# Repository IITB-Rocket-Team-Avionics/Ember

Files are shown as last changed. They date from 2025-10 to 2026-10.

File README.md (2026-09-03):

# Ember
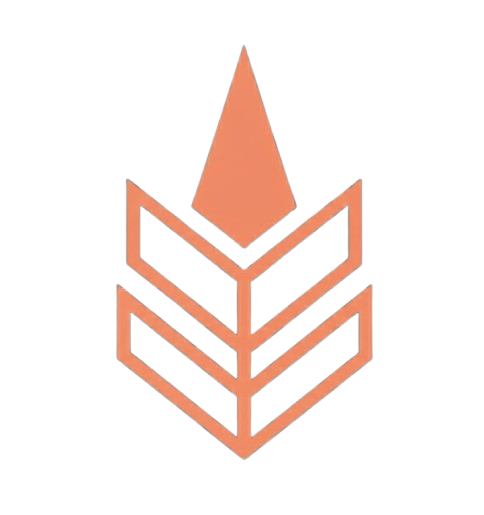
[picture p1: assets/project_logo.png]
Project Logo


Ember is the SRAD flight computer system of the IITB Rocket Team, developed as an experimental platform with mitigations for issues faced by previous systems and as a testbed for new avionics architecture.

## Version Descriptions

### Ember Pilot
Proof of concept version validating new LoRa telemetry and core sensor suite. Features a Raspberry Pi Pico 2 dev board instead of a bare-metal hardware design. All systems validated for future versions.

| Parameter | Details |
|---|---|
| MCU | RP2350A (Pico 2 dev board) |
| Layers | 4 |
| Sensors | BMP280, BNO055, KX134 |
| GNSS | Teseo LIV3F |
| Telemetry | Waveshare Core SX1262 (920MHz LoRa) |

---

### Ember V0.2 (Ember)
First full flight version. Flew successfully at IREC 2026, reaching an apogee of 9,463 ft with a SRAD N-class KNSB motor — 2% overshoot on OpenRocket predicted apogee of 9,272 ft. Split into two boards: Flight Computer Unit (FCU) and Telemetry & Data Unit (TDU).

| Parameter | Details |
|---|---|
| FCU MCU | RP2350A (Pico 2 dev board) |
| TDU MCU | RP2350A (Pico 2 dev board) |
| Layers | 2 |
| Sensors | BMP280, BNO055, KX134, NXP MPXV5100DP |
| GNSS | Quectel L89HA (multi-constellation) |
| Telemetry | Waveshare Core1262 SX1262 (920MHz LoRa) |
| Recovery | Dual deploy — drogue at apogee, main at 400m AGL |
| Pyro channels | 4 (2 primary, 2 redundant) |
| Data logging | External flash |
| COTS backup | EasyMini V2 |

---

### Ember V1 (In Development)
Major architectural redesign with full separation of concerns across dedicated board types. Introduces triple modular redundant recovery, distributed CAN bus architecture, and significantly upgraded data acquisition.

**Board types:**

**NTDU (Navigation, Telemetry & Data Unit)** — main board. Independent sensor suite for navigation and state estimation, GNSS, LoRa telemetry, data acquisition (dp probe, strain gauges), configuration authority for all nodes on boot, aggregates and logs data from all CAN nodes.

| Parameter | Details |
|---|---|
| MCU | STM32H573 |
| Sensors | BMP384, BNO055, KX134, NXP MPXV5100DP (via ADS1220), BX350-3AA strain gauges (via ADS1220) |
| GNSS | Quectel L89HA |
| Telemetry | SX1262 920MHz LoRa |
| Data logging | OctoSPI NOR flash + microSD |
| Communication | CAN bus (all nodes) |
| Power | 2S Li-ion, AP63205WU buck (5V) |

**RU (Recovery Unit) — x3** — dedicated recovery boards in triple modular redundant configuration. Distributed 2-of-3 voting via CAN bus. Each board independently detects apogee and participates in consensus voting.

| Parameter | Details |
|---|---|
| MCU | STM32F411 |
| Sensors | BMP280, single-axis accelerometer |
| Pyro channels | 2 (drogue + main) |
| Communication | CAN bus (shared with NTDU) |
| RTOS | FreeRTOS |
| Power | 1S Li-ion (isolated per board) |
| Voting | 2-of-3 mid-value select consensus |

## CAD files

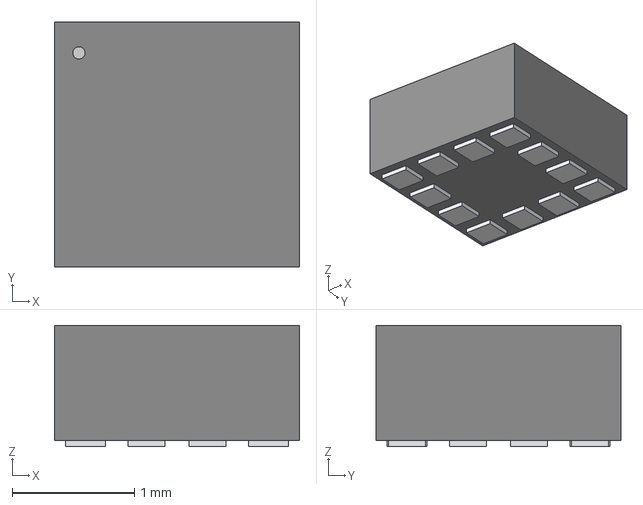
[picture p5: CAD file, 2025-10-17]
EDA_libraries/LGA12_2X2X0P9_ROM.step
2.01 x 2.01 x 0.993 mm

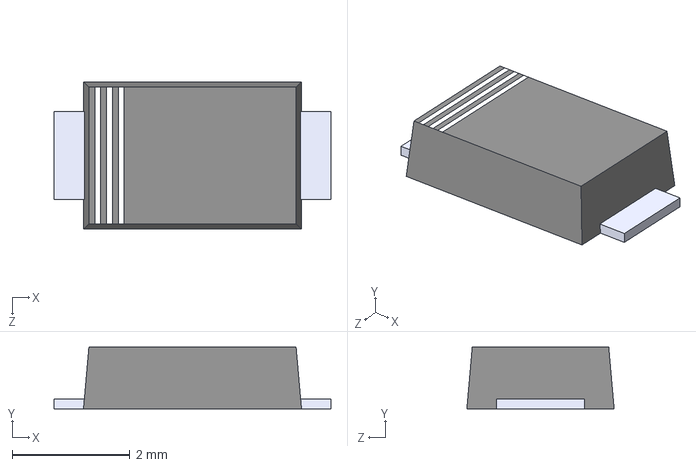
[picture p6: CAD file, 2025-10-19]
EDA_libraries/RSX501LAM20TR/RSX501LAM20TR.step
4.70 x 1.05 x 2.50 mm

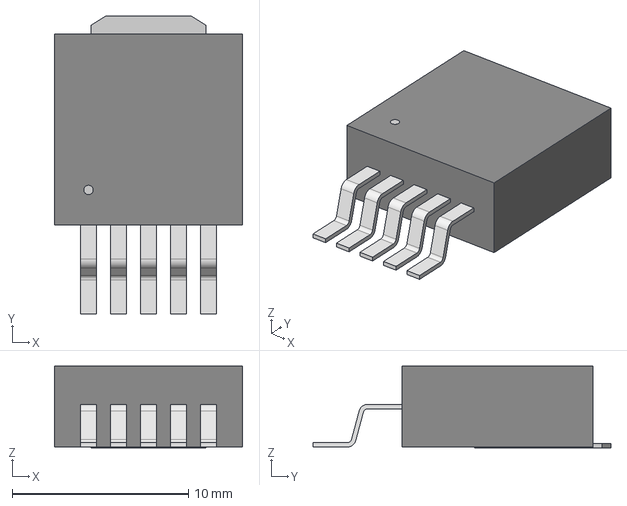
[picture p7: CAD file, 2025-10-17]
EDA_libraries/TO-263-5_MCH.step
10.7 x 16.9 x 4.65 mm

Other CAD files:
assets/project_logo.dxf

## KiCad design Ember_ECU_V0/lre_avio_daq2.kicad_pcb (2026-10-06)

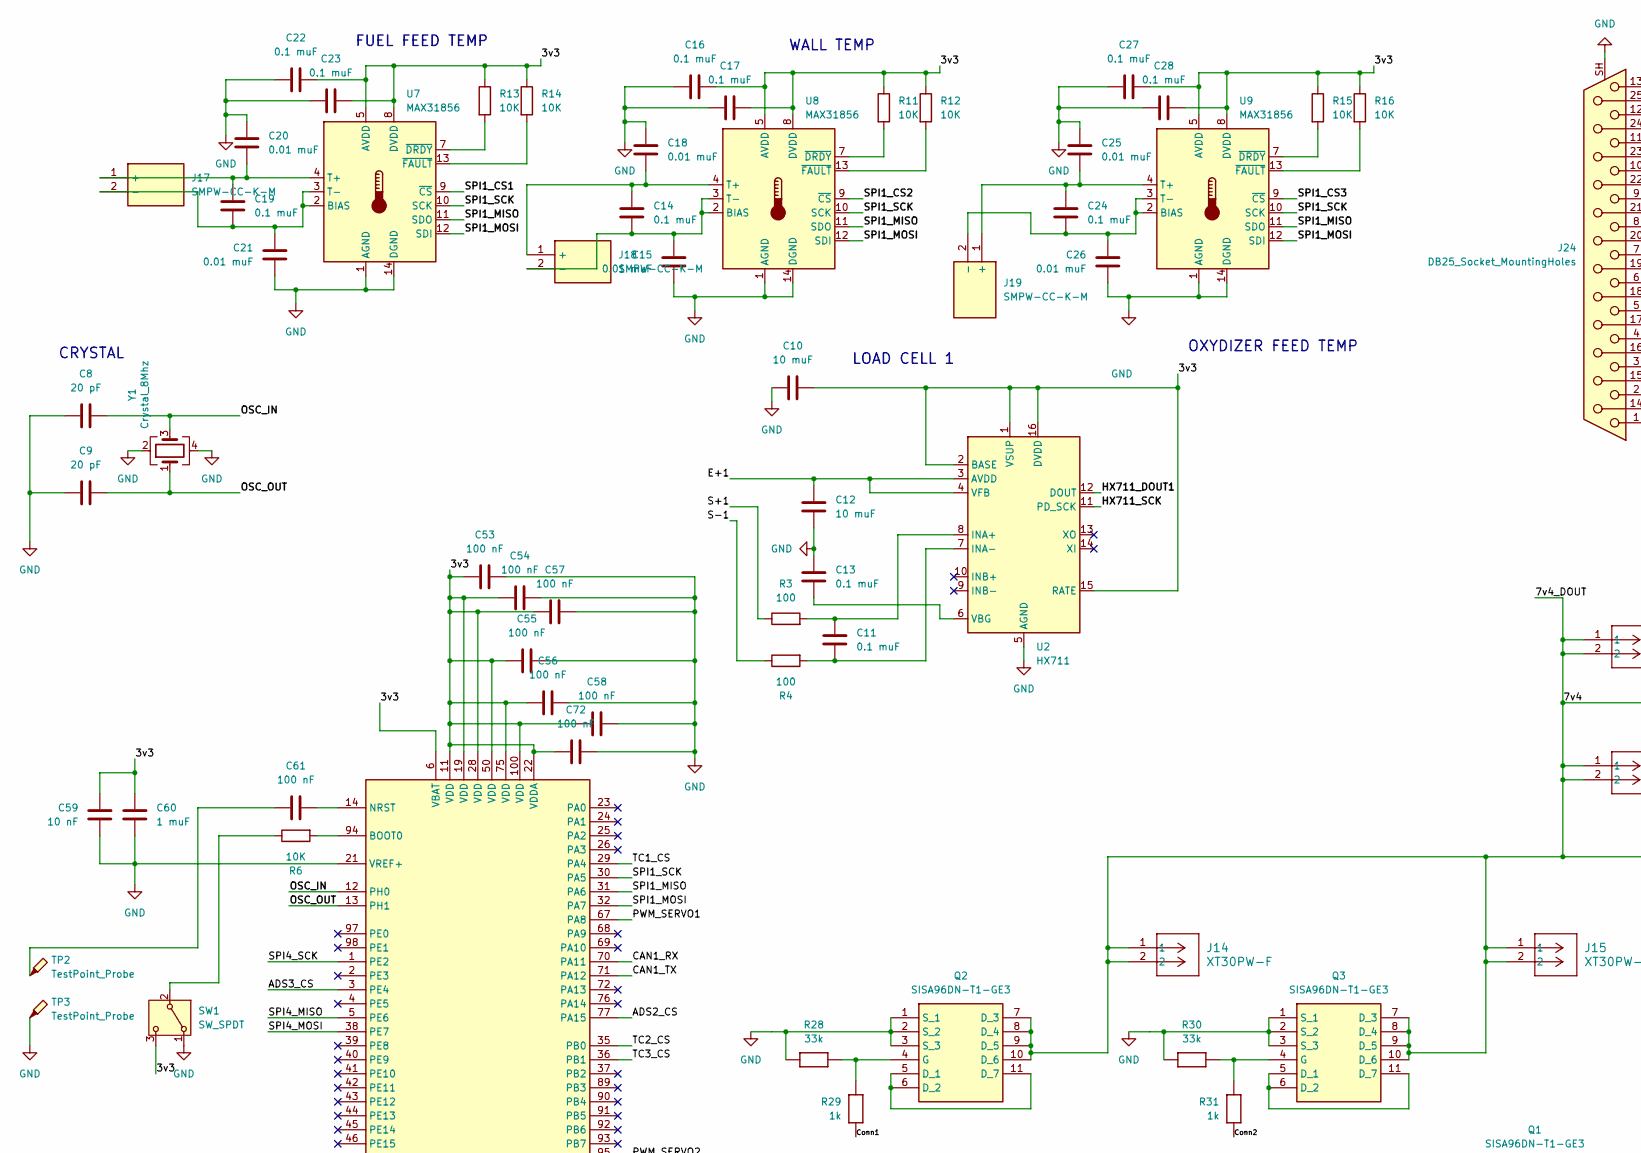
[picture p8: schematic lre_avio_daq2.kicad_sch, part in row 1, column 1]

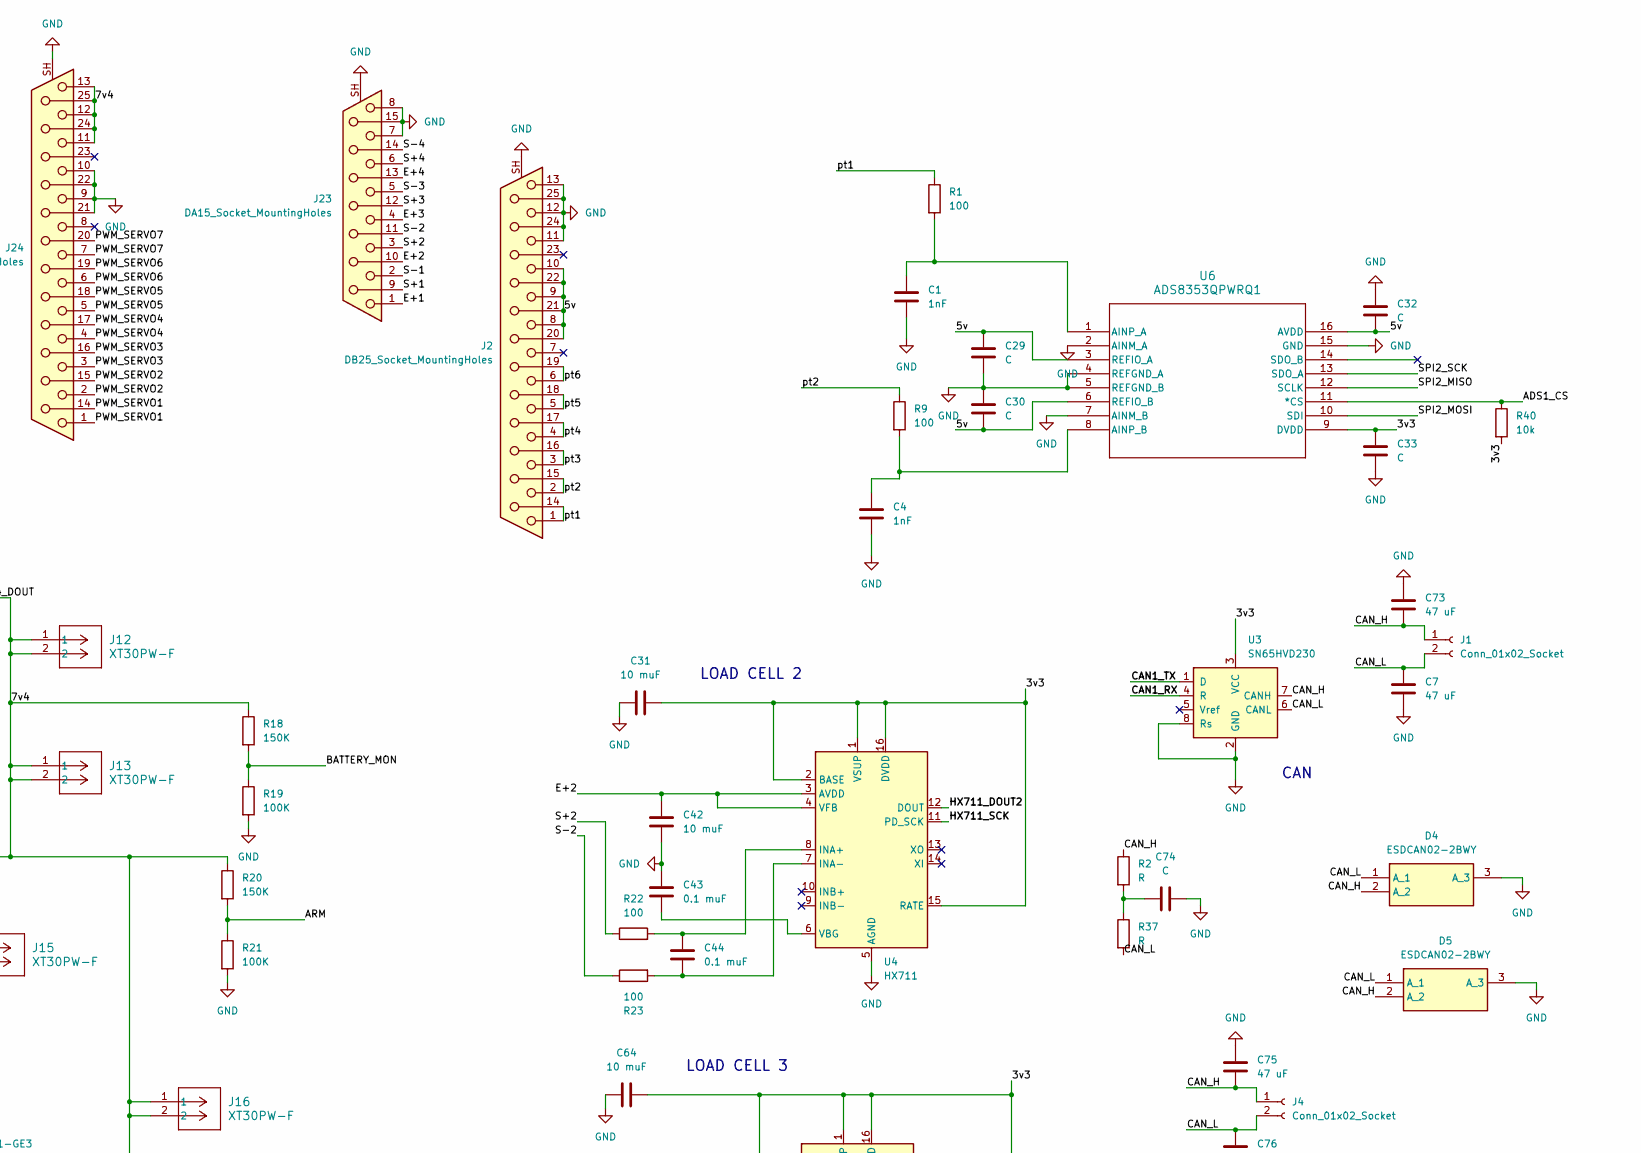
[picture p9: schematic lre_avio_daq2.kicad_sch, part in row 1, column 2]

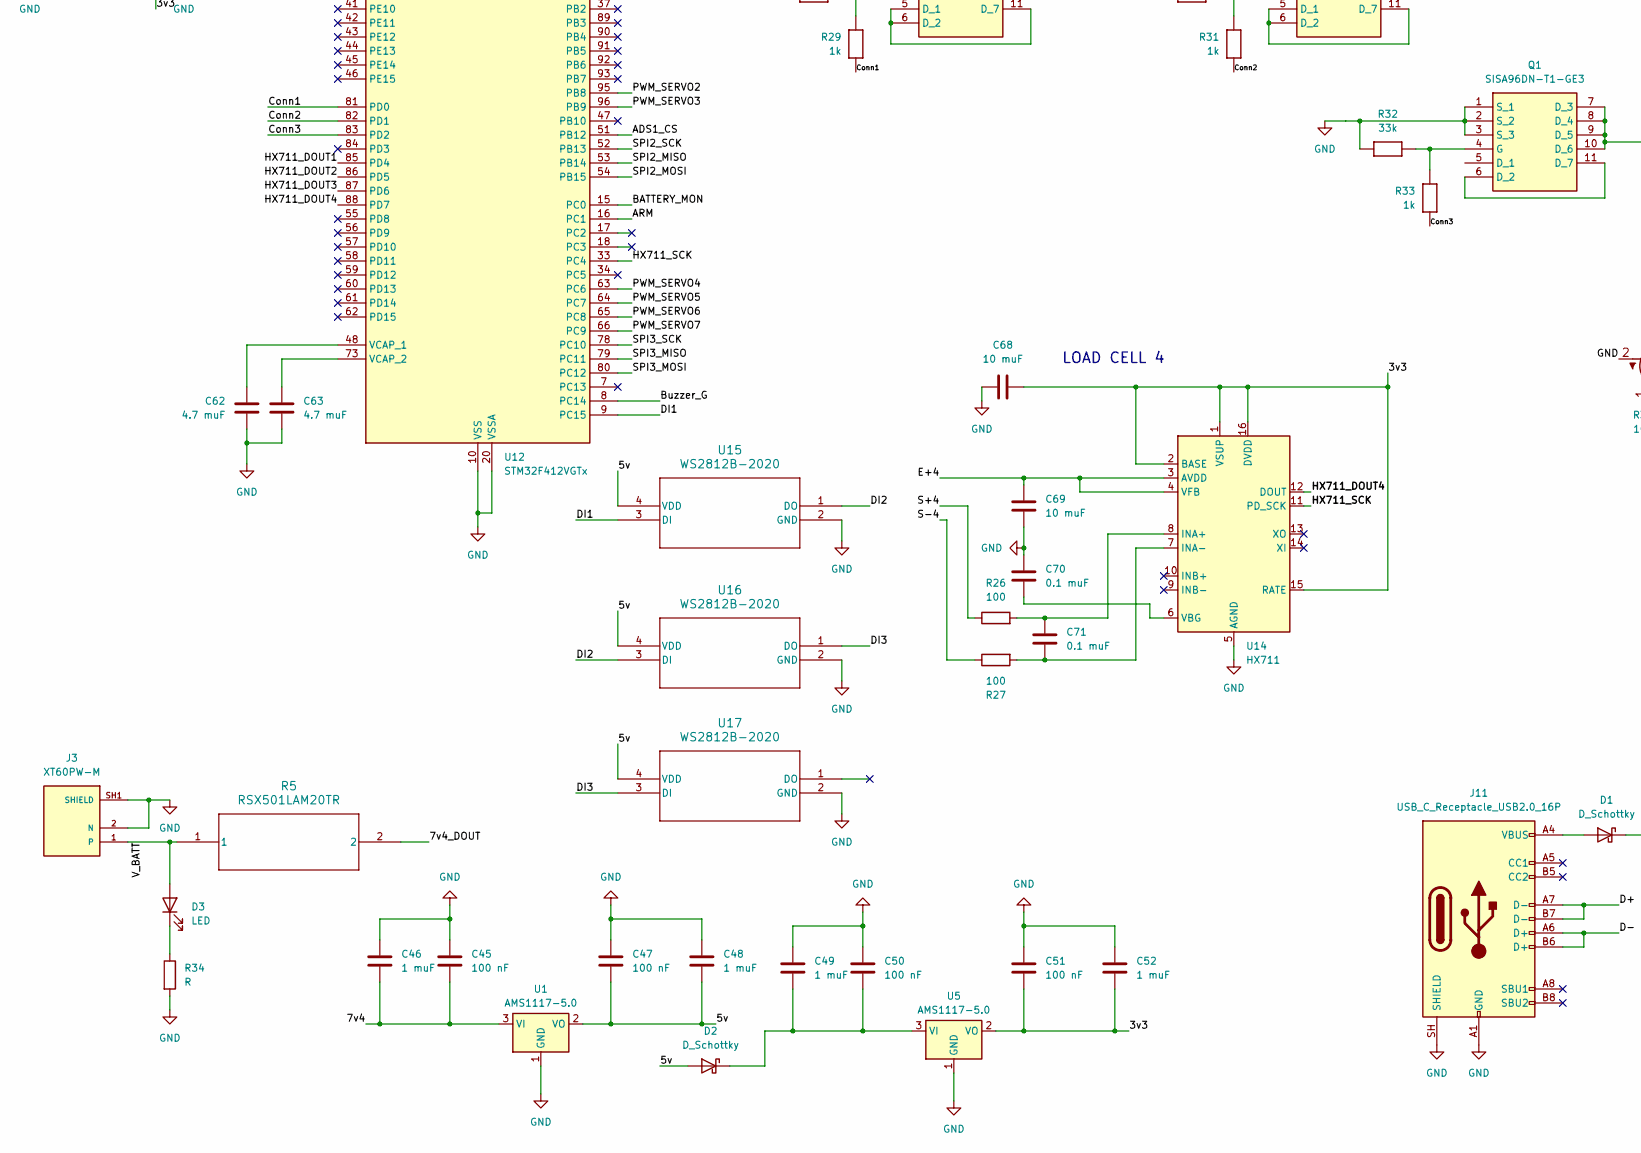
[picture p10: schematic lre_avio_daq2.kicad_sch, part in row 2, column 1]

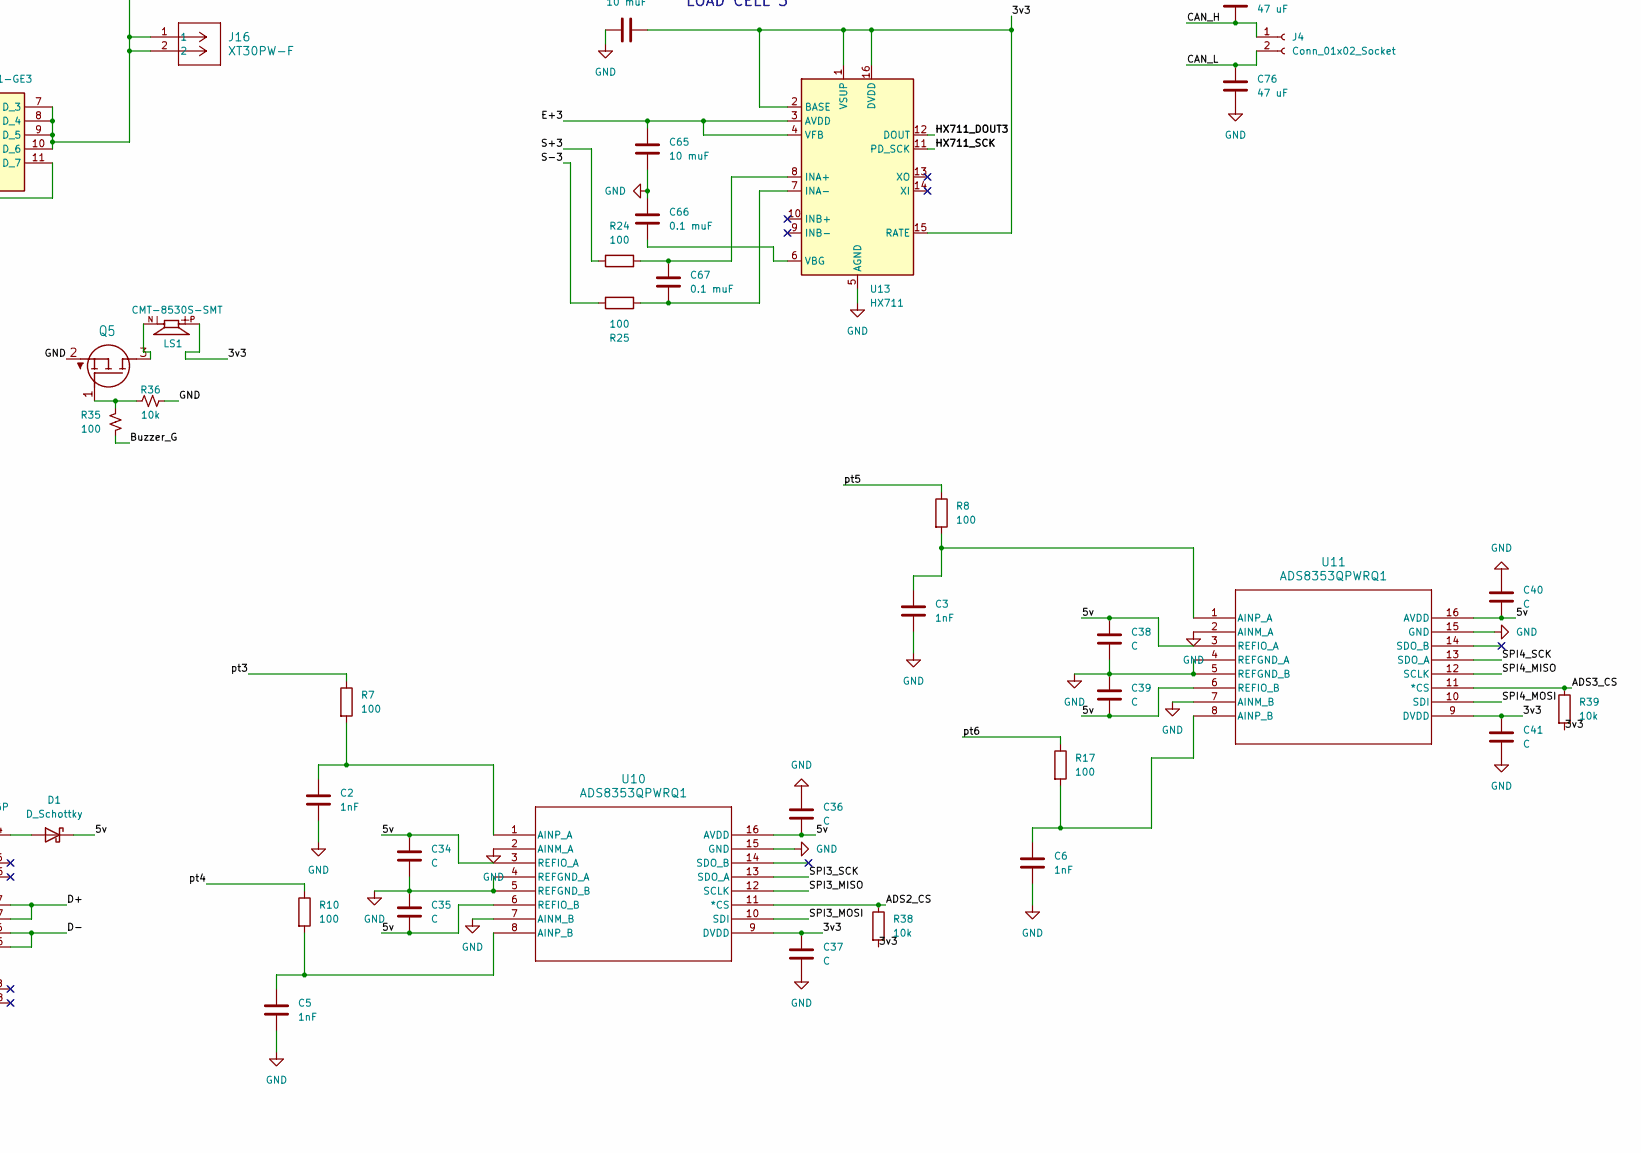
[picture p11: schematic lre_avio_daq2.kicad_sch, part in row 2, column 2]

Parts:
C1, C2, C3, C4, C5, C6: 1nF; C_0603_1608Metric
C7, C73, C75, C76: 47 uF; C_0603_1608Metric
C8, C9: 20 pF; C_0603_1608Metric
C10, C12, C31, C42, C64, C65, C68, C69: 10 muF; C_0603_1608Metric
C11, C13, C14, C16, C17, C19, C22, C23, C24, C27, C28, C43, C44, C66, C67, C70, C71: 0.1 muF; C_0603_1608Metric
C15, C18, C20, C21, C25, C26: 0.01 muF; C_0603_1608Metric
C29, C30, C32, C33, C34, C35, C36, C37, C38, C39, C40, C41, C74: C; C_0603_1608Metric
C45, C47, C50, C51, C53, C54, C55, C56, C57, C58, C61, C72: 100 nF; C_0603_1608Metric
C46, C48, C49, C52, C60: 1 muF; C_0603_1608Metric
C59: 10 nF; C_0603_1608Metric
C62, C63: 4.7 muF; C_0603_1608Metric
D1, D2: D_Schottky; DIO_RB050LAM_ROM
D3: LED; LED_0603_1608Metric
D4, D5: ESDCAN02-2BWY; SOT65P210X110-3N; Manufacturer_Part_Number ESDCAN02-2BWY; Mouser Part Number 511-ESDCAN02-2BWY
J1, J4: Conn_01x02_Socket; JST_EH_B2B-EH-A_1x02_P2.50mm_Vertical
J2, J24: DB25_Socket_MountingHoles; DSUB-25_Socket_Horizontal_P2.77x2.84mm_EdgePinOffset4.94mm_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
J3: XT60PW-M; AMASS_XT60PW-M; PARTREV 1.2
J11: USB_C_Receptacle_USB2.0_16P; USB_C_Receptacle_Amphenol_12401948E412A
J12, J13, J14, J15, J16: XT30PW-F; CONN_XT30PW-F_AMA
J17, J18, J19: SMPW-CC-K-M; SMPWCCKM; Manufacturer_Part_Number SMPW-CC-K-M
J23: DA15_Socket_MountingHoles; DSUB-15_Socket_Horizontal_P2.77x2.84mm_EdgePinOffset4.94mm_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
LS1: CMT-8530S-SMT; CUI_CMT-8530S-SMT
Q1, Q2, Q3: SISA96DN-T1-GE3; SIS862DNT1GE3; Manufacturer_Part_Number SISA96DN-T1-GE3; Mouser Part Number 78-SISA96DN-T1-GE3
Q5: SOT95P240X115-3N
R1, R3, R4, R7, R8, R9, R10, R17, R22, R23, R24, R25, R26, R27, R35: 100; R_0603_1608Metric
R2, R34, R37: R; R_0603_1608Metric
R5: RSX501LAM20TR; R_0603_1608Metric
R6, R11, R12, R13, R14, R15, R16: 10K; R_0603_1608Metric
R18, R20: 150K; R_0603_1608Metric
R19, R21: 100K; R_0603_1608Metric
R28, R30, R32: 33k; R_0603_1608Metric
R29, R31, R33: 1k; R_0603_1608Metric
R36, R38, R39, R40: 10k; R_0603_1608Metric
SW1: SW_SPDT; SW_SPDT_PCM12
TP2, TP3: TestPoint_Probe; TestPoint_Pad_D1.5mm
U1, U5: AMS1117-5.0; SOT-223-3_TabPin2
U2, U4, U13, U14: HX711; SOIC-16_3.9x9.9mm_P1.27mm
U3: SN65HVD230; SOIC-8_3.9x4.9mm_P1.27mm
U6, U10, U11: ADS8353QPWRQ1; TSSOP16_PW_TEX-L
U7, U8, U9: MAX31856; TSSOP-14_4.4x5mm_P0.65mm
U12: STM32F412VGTx; LQFP-100_14x14mm_P0.5mm
U15, U16, U17: WS2812B-2020; SMT_12B-2020_WDS
Y1: Crystal_8Mhz; Crystal_SMD_7050-4Pin_7.0x5.0mm

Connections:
/3v3: C10.2, C16.2, C17.2, C22.2, C23.2, C27.2, C28.2, C31.2, C33.1, C37.1, C41.1, C51.2, C52.2, C53.1, C54.1, C55.1, C56.1, C57.1, C58.1, C59.1, C60.1, C64.2, C68.2, C72.2, LS1.P, R11.1, R12.1, R13.1, R14.1, R15.1, R16.1, R38.2, R39.2, R40.2, SW1.3 (C), U2.1 (VSUP), U2.2 (BASE), U2.15 (RATE), U2.16 (DVDD), U3.3 (VCC), U4.1 (VSUP), U4.2 (BASE), U4.15 (RATE), U4.16 (DVDD), U5.2 (VO), U6.9 (DVDD), U7.5 (AVDD), U7.8 (DVDD), U8.5 (AVDD), U8.8 (DVDD), U9.5 (AVDD), U9.8 (DVDD), U10.9 (DVDD), U11.9 (DVDD), U12.6 (VBAT), U12.11 (VDD), U12.19 (VDD), U12.22 (VDDA), U12.28 (VDD), U12.50 (VDD), U12.75 (VDD), U12.100 (VDD), U13.1 (VSUP), U13.2 (BASE), U13.15 (RATE), U13.16 (DVDD), U14.1 (VSUP), U14.2 (BASE), U14.15 (RATE), U14.16 (DVDD)
/5v: C29.2, C30.2, C32.2, C34.2, C35.2, C36.2, C38.2, C39.2, C40.2, C47.2, C48.2, D1.1 (K), D2.2 (A), J2.8, J2.9, J2.10, J2.20, J2.21, J2.22, U1.2 (VO), U6.3 (REFIO_A), U6.6 (REFIO_B), U6.16 (AVDD), U10.3 (REFIO_A), U10.6 (REFIO_B), U10.16 (AVDD), U11.3 (REFIO_A), U11.6 (REFIO_B), U11.16 (AVDD), U15.4 (VDD), U16.4 (VDD), U17.4 (VDD)
/7v4: C45.2, C46.2, J12.1, J12.2, J13.1, J13.2, J14.1, J14.2, J15.1, J15.2, J16.1, J16.2, J24.11, J24.12, J24.13, J24.24, J24.25, Q1.7 (D_3), Q1.8 (D_4), Q1.9 (D_5), Q1.10 (D_6), Q2.7 (D_3), Q2.8 (D_4), Q2.9 (D_5), Q2.10 (D_6), Q3.7 (D_3), Q3.8 (D_4), Q3.9 (D_5), Q3.10 (D_6), R5.2, R18.1, R20.1, U1.3 (VI)
/ADS1_CS: R40.1, U6.11 (*CS), U12.51 (PB12)
/ADS2_CS: R38.1, U10.11 (*CS), U12.77 (PA15)
/ADS3_CS: R39.1, U11.11 (*CS), U12.3 (PE4)
/ARM: R20.2, R21.1, U12.16 (PC1)
/BATTERY_MON: R18.2, R19.1, U12.15 (PC0)
/Buzzer_G: R35.2, U12.8 (PC14)
/CAN1_RX: U3.4 (R), U12.70 (PA11)
/CAN1_TX: U3.1 (D), U12.71 (PA12)
/CAN_L: C7.1, C76.1, D4.1 (A_1), D5.1 (A_1), J1.2, J4.2, R37.2, U3.6 (CANL)
/Conn1: R29.1, U12.81 (PD0)
/Conn2: R31.1, U12.82 (PD1)
/Conn3: R33.1, U12.83 (PD2)
/D+: J11.A7 (D-), J11.B7 (D-)
/D-: J11.A6 (D+), J11.B6 (D+)
/DI1: U12.9 (PC15), U15.3 (DI)
/DI2: U15.1 (DO), U16.3 (DI)
/DI3: U16.1 (DO), U17.3 (DI)
/E+1: C12.1, J23.1, U2.3 (AVDD), U2.4 (VFB)
/E+2: C42.1, J23.10, U4.3 (AVDD), U4.4 (VFB)
/E+3: C65.1, J23.4, U13.3 (AVDD), U13.4 (VFB)
/E+4: C69.1, J23.13, U14.3 (AVDD), U14.4 (VFB)
/HX711_DOUT1: U2.12 (DOUT), U12.85 (PD4)
/HX711_DOUT2: U4.12 (DOUT), U12.86 (PD5)
/HX711_DOUT3: U12.87 (PD6), U13.12 (DOUT)
/HX711_DOUT4: U12.88 (PD7), U14.12 (DOUT)
/HX711_SCK: U2.11 (PD_SCK), U4.11 (PD_SCK), U12.33 (PC4), U13.11 (PD_SCK), U14.11 (PD_SCK)
/OSC_IN: C8.2, U12.12 (PH0), Y1.3
/OSC_OUT: C9.2, U12.13 (PH1), Y1.1
/PWM_SERVO1: J24.1, J24.14, U12.67 (PA8)
/PWM_SERVO2: J24.2, J24.15, U12.95 (PB8)
/PWM_SERVO3: J24.3, J24.16, U12.96 (PB9)
/PWM_SERVO4: J24.4, J24.17, U12.63 (PC6)
/PWM_SERVO5: J24.5, J24.18, U12.64 (PC7)
/PWM_SERVO6: J24.6, J24.19, U12.65 (PC8)
/PWM_SERVO7: J24.7, J24.20, U12.66 (PC9)
/S+1: J23.9, R3.1
/S+2: J23.3, R22.1
/S+3: J23.12, R24.1
/S+4: J23.6, R26.1
/S-1: J23.2, R4.1
/S-2: J23.11 (P111), R23.1
/S-3: J23.5, R25.1
/S-4: J23.14, R27.1
/SPI1_CS1: U7.9 (~CS)
/SPI1_CS2: U8.9 (~CS)
/SPI1_CS3: U9.9 (~CS)
/SPI1_MISO: U7.11 (SDO), U8.11 (SDO), U9.11 (SDO), U12.31 (PA6)
/SPI1_MOSI: U7.12 (SDI), U8.12 (SDI), U9.12 (SDI), U12.32 (PA7)
/SPI1_SCK: U7.10 (SCK), U8.10 (SCK), U9.10 (SCK), U12.30 (PA5)
/SPI2_MISO: U6.12 (SCLK), U12.53 (PB14)
/SPI2_MOSI: U6.10 (SDI), U12.54 (PB15)
/SPI2_SCK: U6.13 (SDO_A), U12.52 (PB13)
/SPI3_MISO: U10.12 (SCLK), U12.79 (PC11)
/SPI3_MOSI: U10.10 (SDI), U12.80 (PC12)
/SPI3_SCK: U10.13 (SDO_A), U12.78 (PC10)
/SPI4_MISO: U11.12 (SCLK), U12.5 (PE6)
/SPI4_MOSI: U11.10 (SDI), U12.38 (PE7)
/SPI4_SCK: U11.13 (SDO_A), U12.1 (PE2)
/TC1_CS: U12.29 (PA4)
/TC2_CS: U12.35 (PB0)
/TC3_CS: U12.36 (PB1)
/V_BATT: D3.2 (A), J3.1, R5.1
/pt1: J2.1, J2.14, R1.1
/pt2: J2.2, J2.15, R9.1
/pt3: J2.3, J2.16, R7.1
/pt4: J2.4, J2.17, R10.1
/pt5: J2.5, J2.18, R8.1
/pt6: J2.6, J2.19, R17.1
GND: C1.2, C2.2, C3.2, C4.2, C5.2, C6.2, C7.2, C8.1, C9.1, C10.1, C12.2, C13.1, C15.2, C16.1, C17.1, C18.1, C20.1, C21.2, C22.1, C23.1, C25.1, C26.2, C27.1, C28.1, C29.1, C30.1, C31.1, C32.1, C33.2, C34.1, C35.1, C36.1, C37.2, C38.1, C39.1, C40.1, C41.2, C42.2, C43.1, C45.1, C46.1, C47.1, C48.1, C49.1, C50.1, C51.1, C52.1, C53.2, C54.2, C55.2, C56.2, C57.2, C58.2, C59.2, C60.2, C62.2, C63.2, C64.1, C65.2, C66.1, C68.1, C69.2, C70.1, C72.1, C73.1, C74.2, C75.1, C76.2, D4.3 (A_3), D5.3 (A_3), J2.11, J2.12, J2.13, J2.24, J2.25, J2.SH (PAD), J3.2 (N), J3.SH1 (SHIELD), J3.SH2 (SHIELD), J11.A1 (GND), J11.A12 (GND), J11.B1 (GND), J11.B12 (GND), J11.SH (SHIELD), J23.7, J23.8, J23.15, J23.SH (PAD), J24.9, J24.10, J24.21, J24.22, J24.SH (PAD), Q1.1 (S_1), Q1.2 (S_2), Q1.3 (S_3), Q2.1 (S_1), Q2.2 (S_2), Q2.3 (S_3), Q3.1 (S_1), Q3.2 (S_2), Q3.3 (S_3), Q5.2 (S), R19.2, R21.2, R28.2, R30.2, R32.2, R34.2, R36.1, SW1.1 (A), TP3.1 (1_1), U1.1 (GND), U2.5 (AGND), U3.2 (GND), U3.8 (Rs), U4.5 (AGND), U5.1 (GND), U6.2 (AINM_A), U6.4 (REFGND_A), U6.5 (REFGND_B), U6.7 (AINM_B), U6.15 (GND), U7.1 (AGND), U7.14 (DGND), U8.1 (AGND), U8.14 (DGND), U9.1 (AGND), U9.14 (DGND), U10.2 (AINM_A), U10.4 (REFGND_A), U10.5 (REFGND_B), U10.7 (AINM_B), U10.15 (GND), U11.2 (AINM_A), U11.4 (REFGND_A), U11.5 (REFGND_B), U11.7 (AINM_B), U11.15 (GND), U12.10 (VSS), U12.20 (VSSA), U12.21 (VREF+), U12.27 (VSS), U12.49 (VSS), U12.74 (VSS), U12.99 (VSS), U13.5 (AGND), U14.5 (AGND), U15.2 (GND), U16.2 (GND), U17.2 (GND), Y1.2, Y1.4
unnamed: C61.1, TP2.1 (1_1)
unnamed: D1.2 (A), J11.A4 (VBUS), J11.A9 (VBUS), J11.B4 (VBUS), J11.B9 (VBUS)
unnamed: C49.2, C50.2, D2.1 (K), U5.3 (VI)
unnamed: D3.1 (K), R34.1
unnamed: C19.1, C20.2, J17.1 (+), U7.4 (T+)
unnamed: C19.2, C21.1, J17.2 (-), U7.2 (BIAS), U7.3 (T-)
unnamed: C14.1, C18.2, J18.1 (+), U8.4 (T+)
unnamed: C14.2, C15.1, J18.2 (-), U8.2 (BIAS), U8.3 (T-)
unnamed: C24.1, C25.2, J19.1 (+), U9.4 (T+)
unnamed: C24.2, C26.1, J19.2 (-), U9.2 (BIAS), U9.3 (T-)
unnamed: Q1.6 (D_2), Q1.11 (D_7)
unnamed: Q1.4 (G), R32.1, R33.2
unnamed: Q2.5 (D_1), Q2.6 (D_2), Q2.11 (D_7)
unnamed: Q2.4 (G), R28.1, R29.2
unnamed: Q3.5 (D_1), Q3.6 (D_2), Q3.11 (D_7)
unnamed: Q3.4 (G), R30.1, R31.2
unnamed: LS1.N, Q5.3 (D)
unnamed: Q5.1 (G), R35.1, R36.2
unnamed: R6.1, SW1.2 (B)
unnamed: C11.1, R3.2, U2.8 (INA+)
unnamed: C11.2, R4.2, U2.7 (INA-)
unnamed: C13.2, U2.6 (VBG)
unnamed: C44.1, R22.2, U4.8 (INA+)
unnamed: C44.2, R23.2, U4.7 (INA-)
unnamed: C43.2, U4.6 (VBG)
unnamed: C1.1, R1.2, U6.1 (AINP_A)
unnamed: C4.1, R9.2, U6.8 (AINP_B)
unnamed: R13.2, U7.7 (~DRDY)
unnamed: R14.2, U7.13 (~FAULT)
unnamed: R11.2, U8.7 (~DRDY)
unnamed: R12.2, U8.13 (~FAULT)
unnamed: R15.2, U9.7 (~DRDY)
unnamed: R16.2, U9.13 (~FAULT)
unnamed: C2.1, R7.2, U10.1 (AINP_A)
unnamed: C5.1, R10.2, U10.8 (AINP_B)
unnamed: C3.1, R8.2, U11.1 (AINP_A)
unnamed: C6.1, R17.2, U11.8 (AINP_B)
unnamed: R6.2, U12.94 (BOOT0)
unnamed: C61.2, U12.14 (NRST)
unnamed: C62.1, U12.48 (VCAP_1)
unnamed: C63.1, U12.73 (VCAP_2)
unnamed: C67.1, R24.2, U13.8 (INA+)
unnamed: C67.2, R25.2, U13.7 (INA-)
unnamed: C66.2, U13.6 (VBG)
unnamed: C71.1, R26.2, U14.8 (INA+)
unnamed: C71.2, R27.2, U14.7 (INA-)
unnamed: C70.2, U14.6 (VBG)

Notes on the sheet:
LOAD CELL 1
CRYSTAL
LOAD CELL 2
LOAD CELL 3
FUEL FEED TEMP
LOAD CELL 4
CAN
OXYDIZER FEED TEMP
WALL TEMP

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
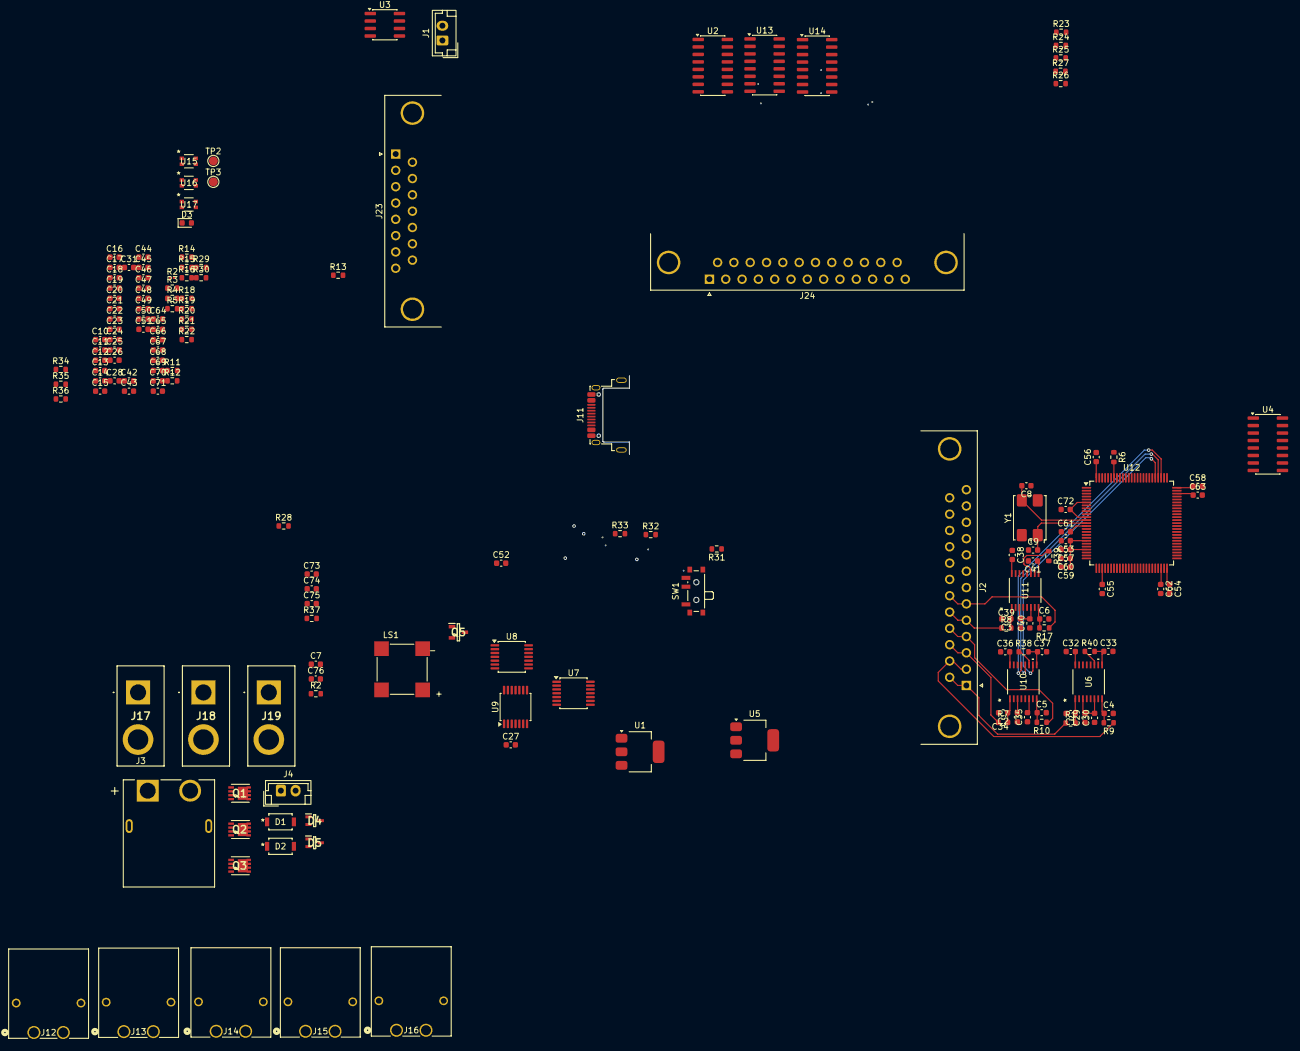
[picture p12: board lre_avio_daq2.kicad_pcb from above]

Board: 4 copper layers, 163 parts (0 on the bottom side), 115 nets.

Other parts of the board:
R2#2: R; R_0603_1608Metric

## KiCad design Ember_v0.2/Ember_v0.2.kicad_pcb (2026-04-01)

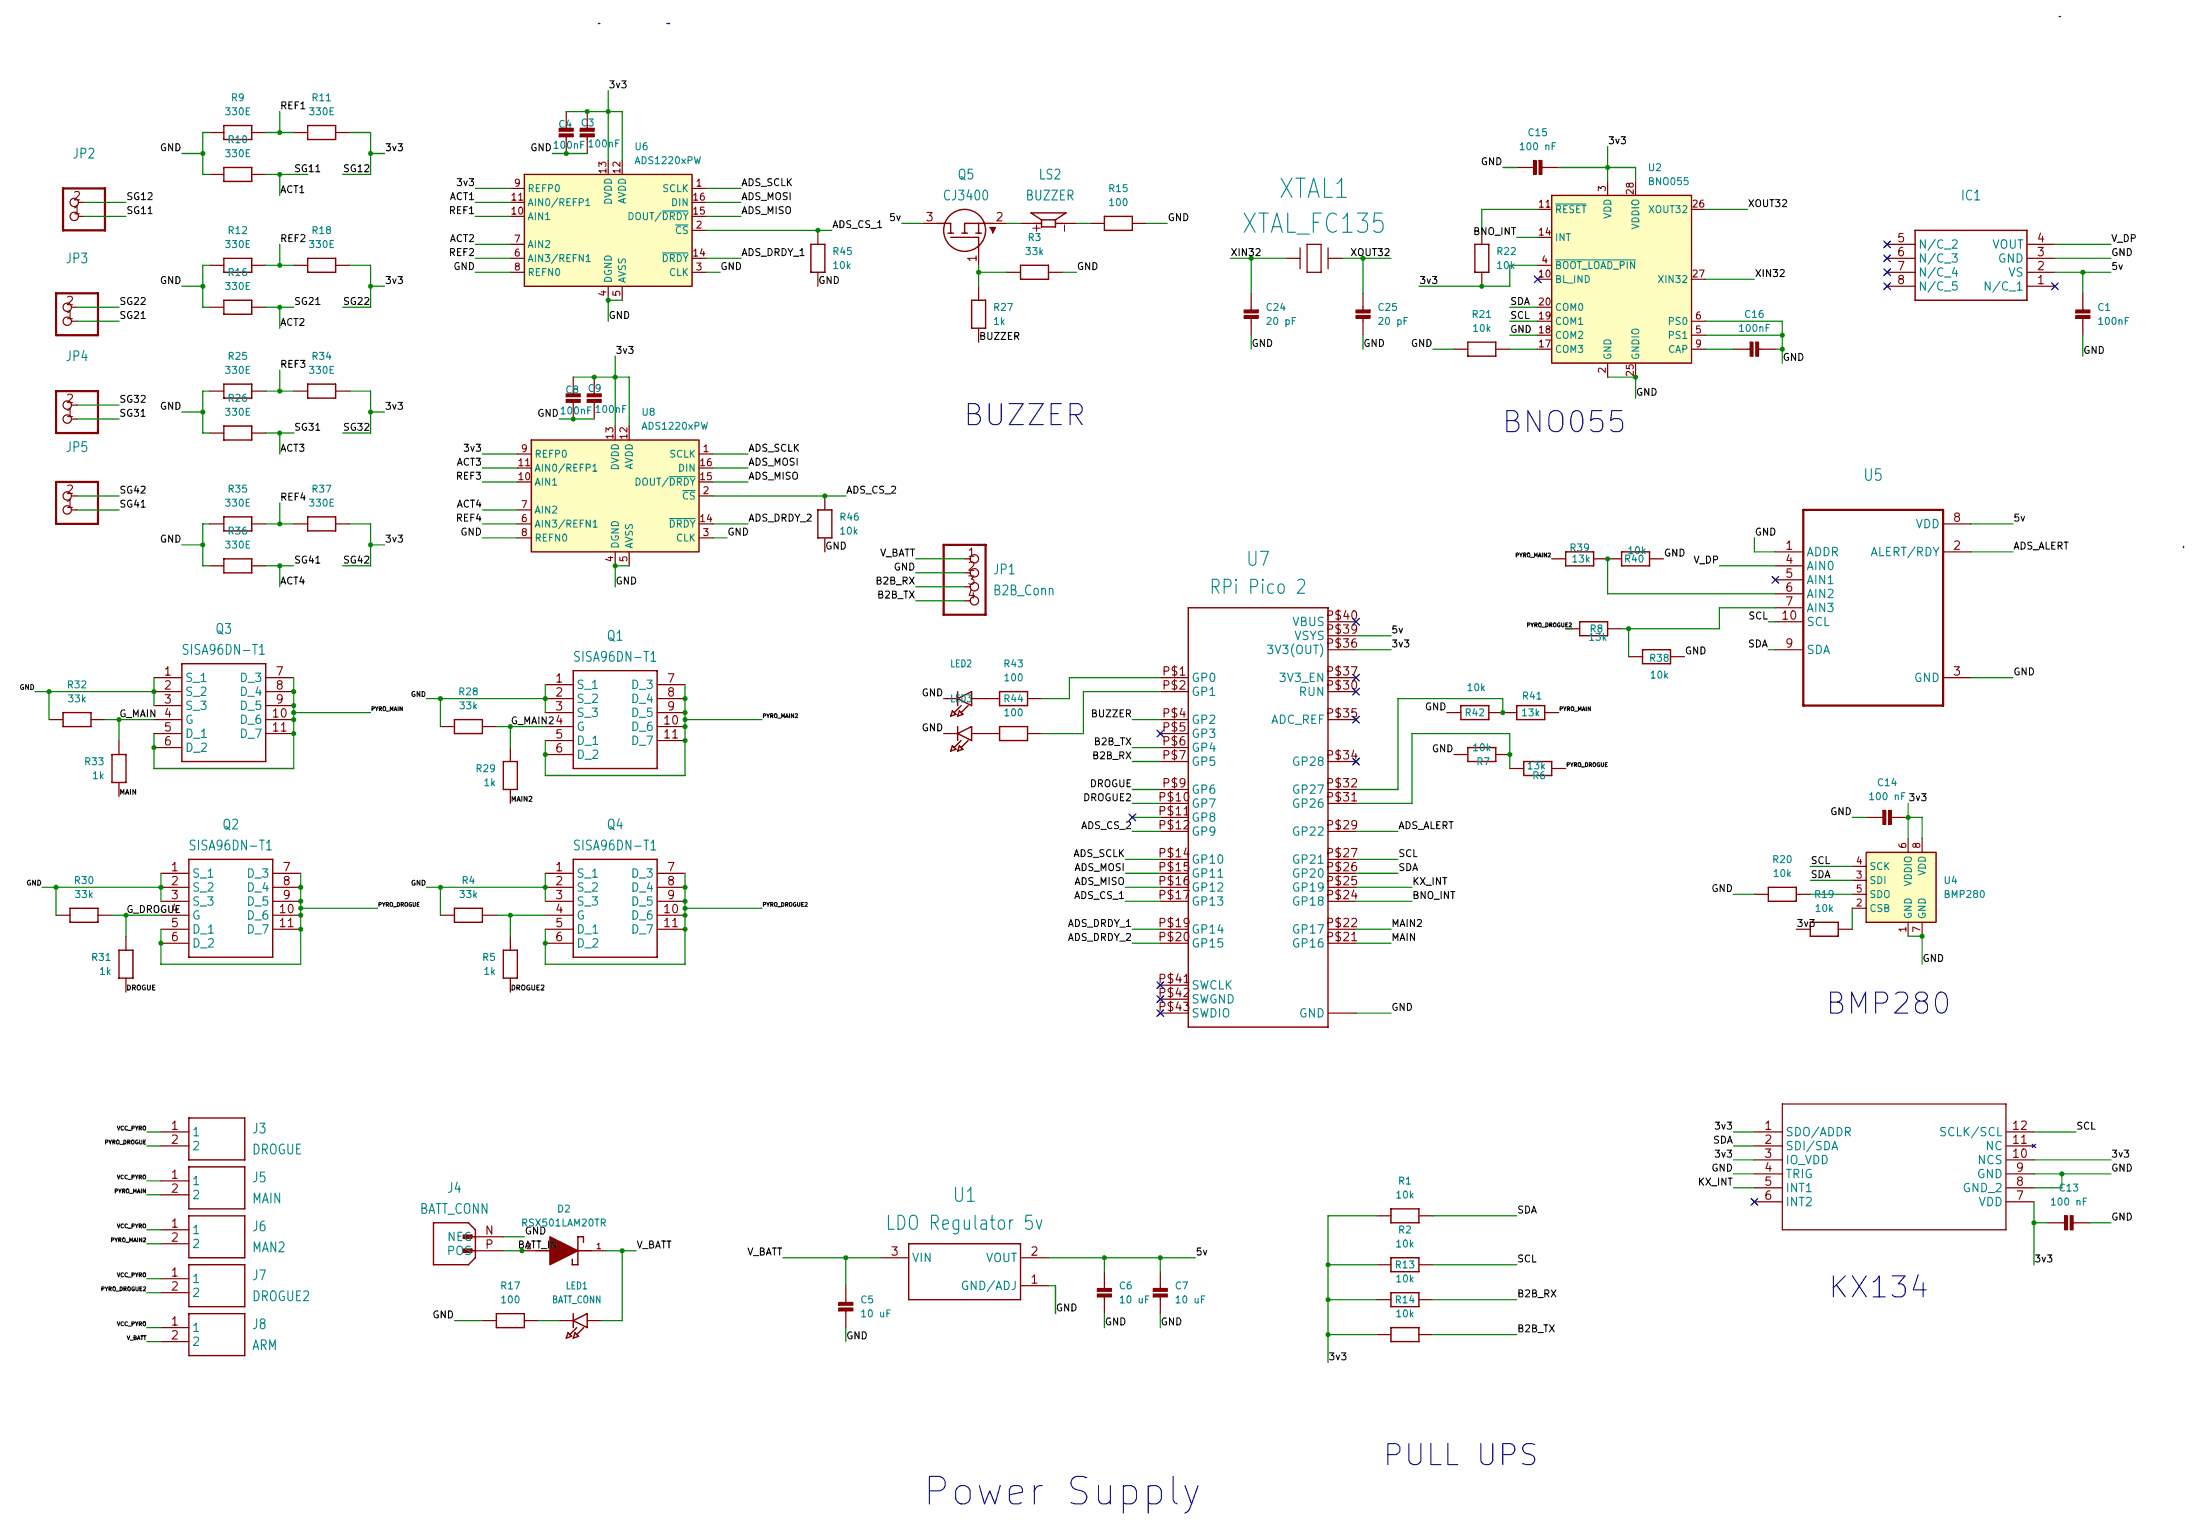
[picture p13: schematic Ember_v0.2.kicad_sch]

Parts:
C1, C3, C4, C8, C9, C16: 100nF; 0603
C5, C6, C7: 10 uF; 0603
C13, C14, C15: 100 nF; 0603
C24, C25: 20 pF; 0603
D2: RSX501LAM20TR; DIOM4725X105N; MOUSER_PART_NUMBER 755-RSX501LAM20TR; DigiKey_Part_Number RSX501LAM20CT-ND
IC1: MPXV5100DP
J3: DROGUE; ONSHORE_OSTTA020161
J4: BATT_CONN; AMASS_XT60-M
J5: MAIN; ONSHORE_OSTTA020161
J6: MAN2; ONSHORE_OSTTA020161
J7: DROGUE2; ONSHORE_OSTTA020161
J8: ARM; ONSHORE_OSTTA020161
JP1: B2B_Conn; 1X04_OVAL
JP2, JP3, JP4, JP5: 1X02_OVAL
LED1: BATT_CONN; CHIPLED_0603
LED2, LED3: CHIPLED_0603
LS2: BUZZER; CUI_CMT-8530S-SMT
Q1, Q2, Q3, Q4: SISA96DN-T1; SIS862DNT1GE3
Q5: CJ3400; SOT95P240X115-3N
R1, R2, R7, R13, R14, R19, R20, R21, R22, R38, R40, R42, R45, R46: 10k; 0603
R3, R4, R28, R30, R32: 33k; 0603
R5, R27, R29, R31, R33: 1k; 0603
R6, R8, R39, R41: 13k; 0603
R9, R10, R11, R12, R16, R18, R25, R26, R34, R35, R36, R37: 330E; 0603
R15, R17, R43, R44: 100; 0603
U1: LDO Regulator 5v; SOT229P700X180-4N
U2: BNO055; LGA-28_5.2x3.8mm_P0.5mm
U3: LGA12_2X2X0P9_ROM
U4: BMP280; Bosch_LGA-8_2x2.5mm_P0.65mm_ClockwisePinNumbering
U5: SOP50P490X110-10N
U6, U8: ADS1220xPW; TSSOP-16_4.4x5mm_P0.65mm
U7: RPi Pico 2; PICO-PKG-SMD
XTAL1: XTAL_FC135; XTAL_FC-135_EPS

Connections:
/3v3: C3.1, C4.1, C8.1, C9.1, C13.2, C14.1, C15.1, JP2.2, JP3.2, JP4.2, JP5.2, R1.1, R2.1, R11.2, R13.1, R14.1, R18.2, R19.1, R22.1, R34.2, R37.2, U2.3 (VDD), U2.4 (~BOOT_LOAD_PIN), U2.28 (VDDIO), U3.1 (SDO/ADDR), U3.3 (IO_VDD), U3.7 (VDD), U3.10 (NCS), U4.6 (VDDIO), U4.8 (VDD), U6.9 (REFP0), U6.12 (AVDD), U6.13 (DVDD), U7.P$36 (3V3(OUT)), U8.9 (REFP0), U8.12 (AVDD), U8.13 (DVDD)
/5v: C1.1, C6.1, C7.1, IC1.2 (VS), Q5.3 (D), U1.2 (VOUT), U5.8 (VDD), U7.P$39 (VSYS)
/ACT1: JP2.1, R10.2, U6.11 (AIN0/REFP1)
/ACT2: JP3.1, R16.2, U6.7 (AIN2)
/ACT3: JP4.1, R26.2, U8.11 (AIN0/REFP1)
/ACT4: JP5.1, R36.2, U8.7 (AIN2)
/ADS_ALERT: U5.2 (ALERT/RDY), U7.P$29 (GP22)
/ADS_CS_1: R45.1, U6.2 (~CS), U7.P$17 (GP13)
/ADS_CS_2: R46.1, U7.P$12 (GP9), U8.2 (~CS)
/ADS_DRDY_1: U6.14 (~DRDY), U7.P$19 (GP14)
/ADS_DRDY_2: U7.P$20 (GP15), U8.14 (~DRDY)
/ADS_MISO: U6.15 (DOUT/~DRDY), U7.P$16 (GP12), U8.15 (DOUT/~DRDY)
/ADS_MOSI: U6.16 (DIN), U7.P$15 (GP11), U8.16 (DIN)
/ADS_SCLK: U6.1 (SCLK), U7.P$14 (GP10), U8.1 (SCLK)
/B2B_RX: JP1.3, R13.2, U7.P$7 (GP5)
/B2B_TX: JP1.4, R14.2, U7.P$6 (GP4)
/BATT_IN: D2.2, J4.P (POS)
/BNO_INT: U2.14 (INT), U7.P$24 (GP18)
/BUZZER: R27.1, U7.P$4 (GP2)
/DROGUE: R31.1, U7.P$9 (GP6)
/DROGUE2: R5.1, U7.P$10 (GP7)
/GND: C1.2, C3.2, C4.2, C5.2, C6.2, C7.2, C8.2, C9.2, C13.1, C14.2, C15.2, C16.1, C24.1, C25.1, IC1.3 (GND), J4.N (NEG), JP1.2, LED2.C, LED3.C, Q1.1 (S_1), Q1.2 (S_2), Q1.3 (S_3), Q2.1 (S_1), Q2.2 (S_2), Q2.3 (S_3), Q3.1 (S_1), Q3.2 (S_2), Q3.3 (S_3), Q4.1 (S_1), Q4.2 (S_2), Q4.3 (S_3), R3.2, R4.2, R7.2, R9.1, R10.1, R12.1, R15.2, R16.1, R17.1, R20.1, R21.1, R25.1, R26.1, R28.2, R30.2, R32.2, R35.1, R36.1, R38.2, R40.2, R42.2, R45.2, R46.2, U1.1 (GND/ADJ), U2.2 (GND), U2.5 (PS1), U2.6 (PS0), U2.18 (COM2), U2.25 (GNDIO), U3.4 (TRIG), U3.8 (GND_2), U3.9 (GND), U4.1 (GND), U4.7 (GND), U5.1 (ADDR), U5.3 (GND), U6.3 (CLK), U6.4 (DGND), U6.5 (AVSS), U6.8 (REFN0), U7.P$3 (GND), U7.P$8 (GND), U7.P$13 (GND), U7.P$18 (GND), U7.P$23 (GND), U7.P$28 (GND), U7.P$33 (GND), U7.P$38 (GND), U8.3 (CLK), U8.4 (DGND), U8.5 (AVSS), U8.8 (REFN0)
/G_DROGUE: Q2.4 (G), R30.1, R31.2
/G_MAIN: Q3.4 (G), R32.1, R33.2
/G_MAIN2: Q1.4 (G), R28.1, R29.2
/KX_INT: U3.5 (INT1), U7.P$25 (GP19)
/MAIN: R33.1, U7.P$21 (GP16)
/MAIN2: R29.1, U7.P$22 (GP17)
/PYRO_DROGUE: J3.2, Q2.5 (D_1), Q2.6 (D_2), Q2.7 (D_3), Q2.8 (D_4), Q2.9 (D_5), Q2.10 (D_6), Q2.11 (D_7), R6.1
/PYRO_DROGUE2: J7.2, Q4.5 (D_1), Q4.6 (D_2), Q4.7 (D_3), Q4.8 (D_4), Q4.9 (D_5), Q4.10 (D_6), Q4.11 (D_7), R8.1
/PYRO_MAIN: J5.2, Q3.5 (D_1), Q3.6 (D_2), Q3.7 (D_3), Q3.8 (D_4), Q3.9 (D_5), Q3.10 (D_6), Q3.11 (D_7), R41.1
/PYRO_MAIN2: J6.2, Q1.5 (D_1), Q1.6 (D_2), Q1.7 (D_3), Q1.8 (D_4), Q1.9 (D_5), Q1.10 (D_6), Q1.11 (D_7), R39.1
/REF1: R9.2, R11.1, U6.10 (AIN1)
/REF2: R12.2, R18.1, U6.6 (AIN3/REFN1)
/REF3: R25.2, R34.1, U8.10 (AIN1)
/REF4: R35.2, R37.1, U8.6 (AIN3/REFN1)
/SCL: R2.2, U2.19 (COM1), U3.12 (SCLK/SCL), U4.4 (SCK), U5.10 (SCL), U7.P$27 (GP21)
/SDA: R1.2, U2.20 (COM0), U3.2 (SDI/SDA), U4.3 (SDI), U5.9 (SDA), U7.P$26 (GP20)
/VCC_PYRO: J3.1, J5.1, J6.1, J7.1, J8.1
/V_BATT: C5.1, D2.1, J8.2, JP1.1, LED1.A, U1.3 (VIN)
/V_DP: IC1.4 (VOUT), U5.4 (AIN0)
/XIN32: C24.2, U2.27 (XIN32), XTAL1.1
/XOUT32: C25.2, U2.26 (XOUT32), XTAL1.2
unnamed: C16.2, U2.9 (CAP)
unnamed: LED1.C, R17.2
unnamed: LED2.A, R43.1
unnamed: LED3.A, R44.1
unnamed: LS2.N, R15.1
unnamed: Q4.4 (G), R4.1, R5.2
unnamed: Q5.1 (G), R3.1, R27.2
unnamed: LS2.P, Q5.2 (S)
unnamed: R21.2, U2.17 (COM3)
unnamed: R22.2, U2.11 (~RESET)
unnamed: R19.2, U4.2 (CSB)
unnamed: R20.2, U4.5 (SDO)
unnamed: R39.2, R40.1, U5.6 (AIN2)
unnamed: R8.2, R38.1, U5.7 (AIN3)
unnamed: R43.2, U7.P$1 (GP0)
unnamed: R44.2, U7.P$2 (GP1)
unnamed: R6.2, R7.1, U7.P$31 (GP26)
unnamed: R41.2, R42.1, U7.P$32 (GP27)

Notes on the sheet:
KX134
BNO055
Power Supply
BUZZER
PULL UPS
BMP280

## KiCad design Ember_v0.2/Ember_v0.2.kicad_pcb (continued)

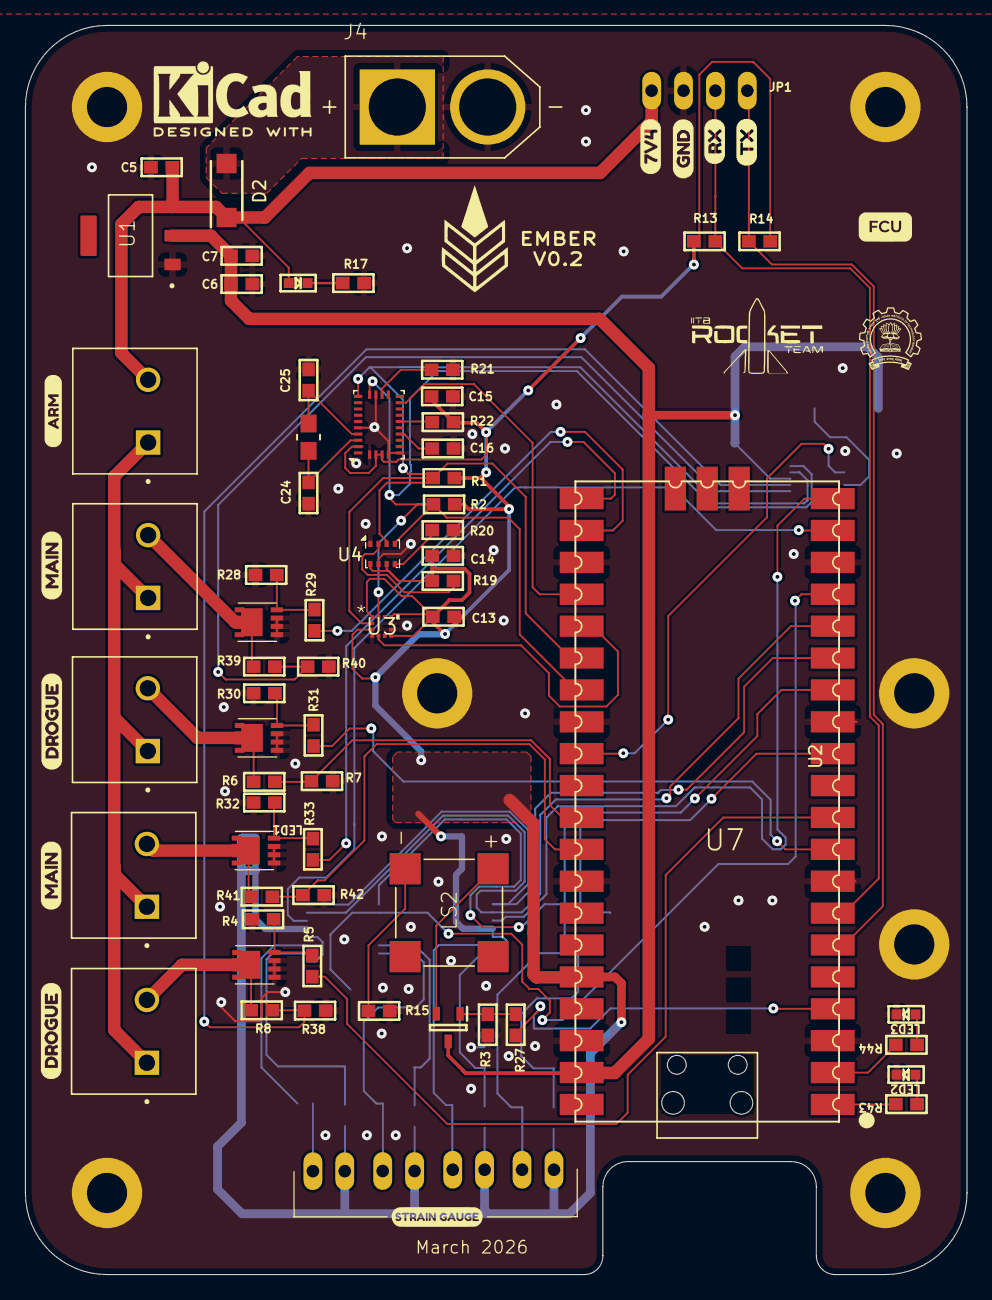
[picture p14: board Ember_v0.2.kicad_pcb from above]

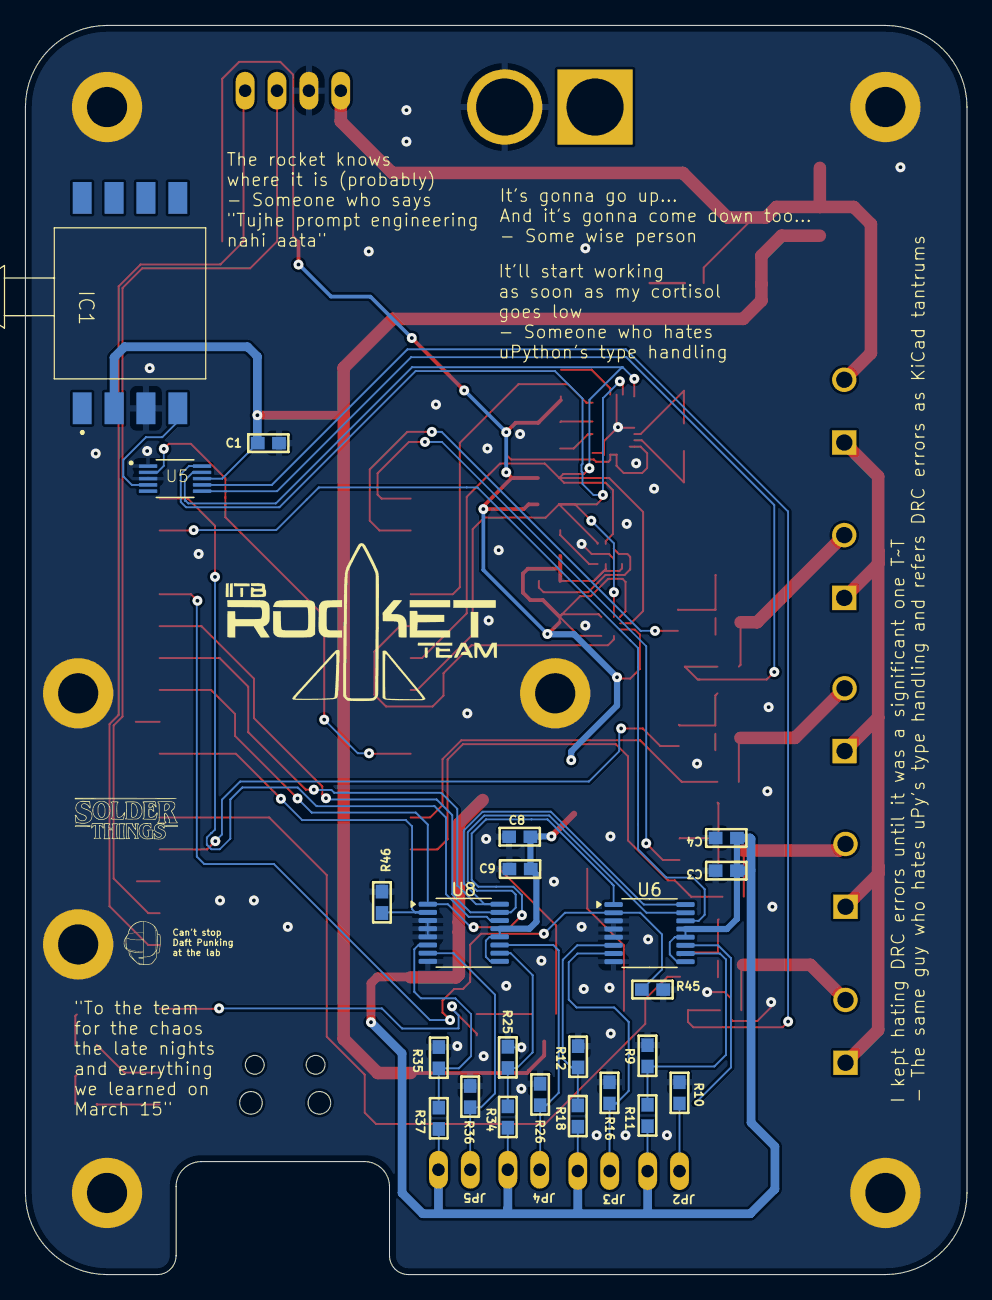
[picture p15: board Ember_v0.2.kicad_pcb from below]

Board: 2 copper layers, 75.0 x 99.5 mm, 89 parts (27 on the bottom side), 61 nets.

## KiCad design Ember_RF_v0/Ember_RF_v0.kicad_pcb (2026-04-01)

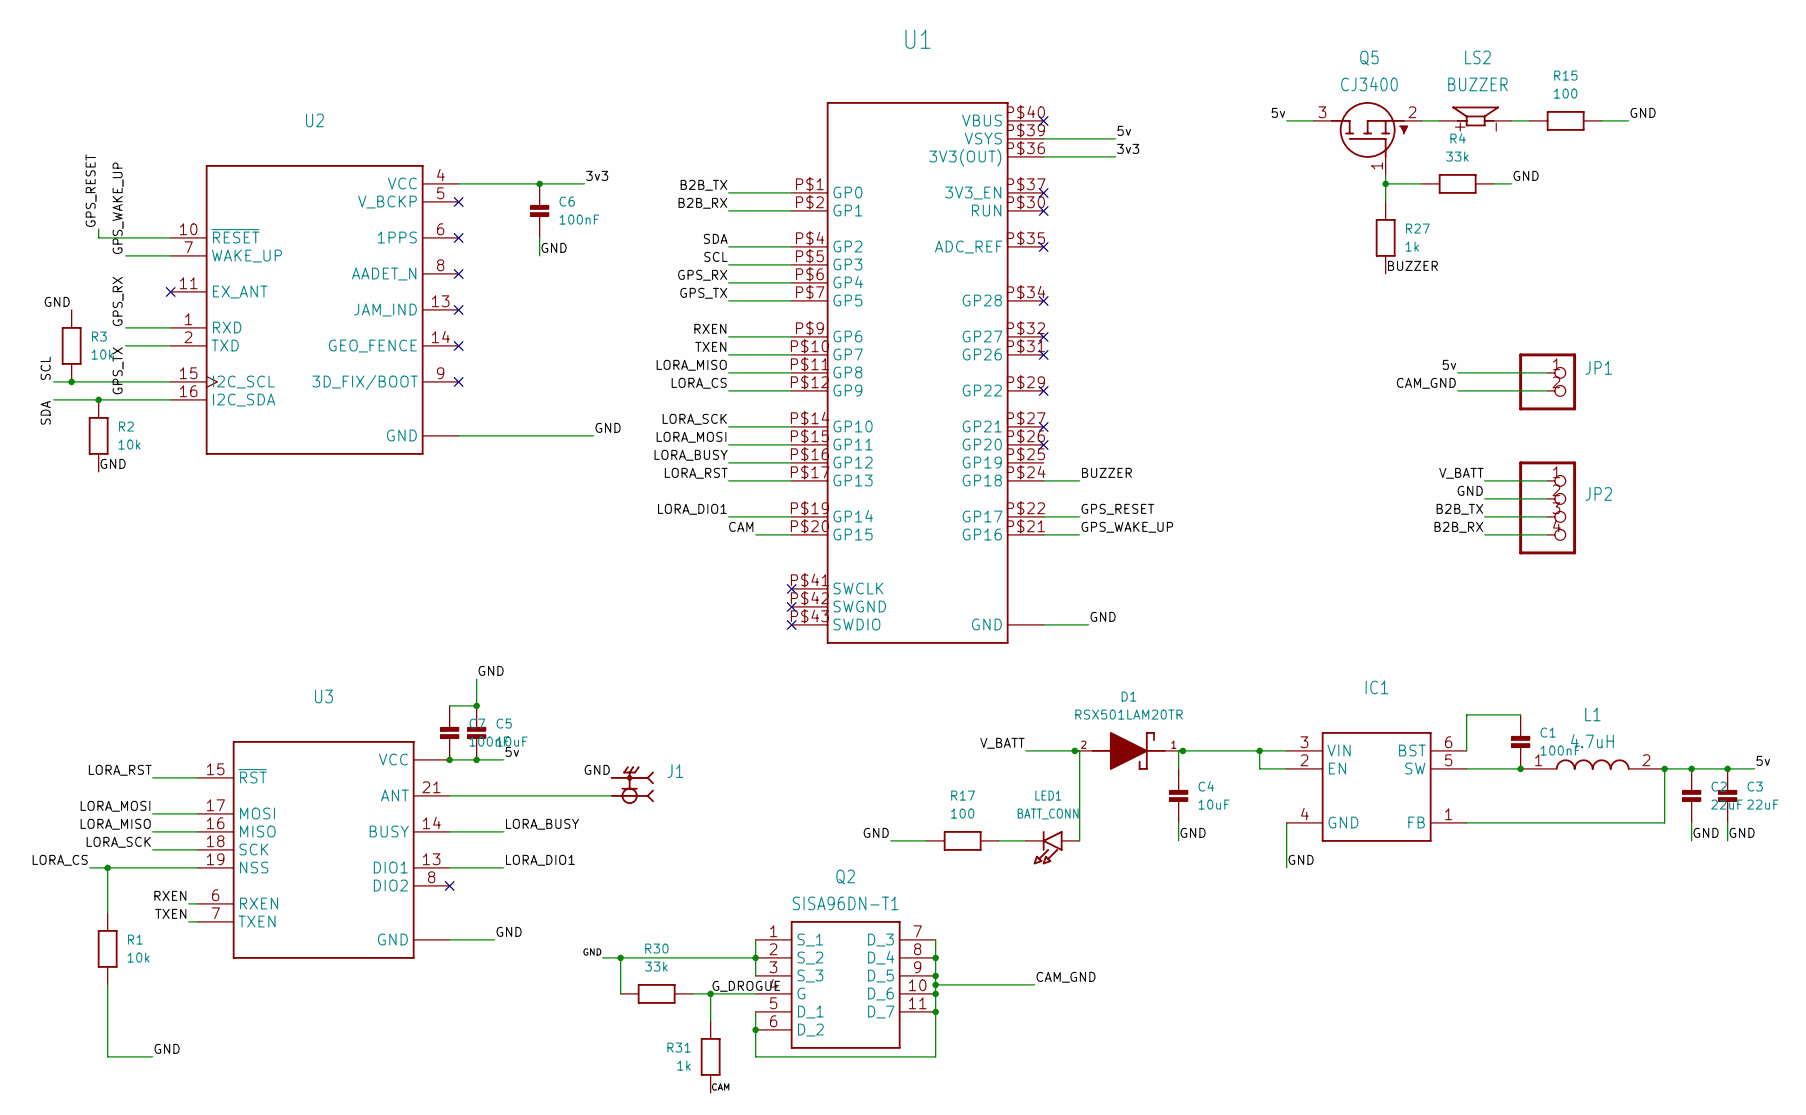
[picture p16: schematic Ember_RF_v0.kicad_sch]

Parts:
C1, C6, C7: 100nF; 0603
C2, C3: 22uF; 0603
C4, C5: 10uF; 0603
D1: RSX501LAM20TR; DIOM4725X105N; MOUSER_PART_NUMBER 755-RSX501LAM20TR; DigiKey_Part_Number RSX501LAM20CT-ND
IC1: SOT95P280X100-6N
J1: RFSOLUTIONS_CON-SMA-EDGE-S
JP1: 1X02_OVAL
JP2: 1X04_OVAL
L1: 4.7uH; INDPM3027X150N
LED1: BATT_CONN; CHIPLED_0603
LS2: BUZZER; CUI_CMT-8530S-SMT
Q2: SISA96DN-T1; SIS862DNT1GE3
Q5: CJ3400; SOT95P240X115-3N
R1, R2, R3: 10k; 0603
R4, R30: 33k; 0603
R15, R17: 100; 0603
R27, R31: 1k; 0603
U1: PICO-PKG-SMD
U2: XCVR_L89
U3: XCVR_E22-900M30S

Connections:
/3v3: C6.1, U1.P$36 (3V3(OUT)), U2.4 (VCC)
/5v: C2.1, C3.1, C5.2, C7.2, IC1.1 (FB), JP1.1, L1.2, Q5.3 (D), U1.P$39 (VSYS), U3.9 (VCC), U3.10 (VCC)
/B2B_RX: JP2.4, U1.P$2 (GP1)
/B2B_TX: JP2.3, U1.P$1 (GP0)
/BUZZER: R27.1, U1.P$24 (GP18)
/CAM: R31.1, U1.P$20 (GP15)
/CAM_GND: JP1.2, Q2.5 (D_1), Q2.6 (D_2), Q2.7 (D_3), Q2.8 (D_4), Q2.9 (D_5), Q2.10 (D_6), Q2.11 (D_7)
/GND: C2.2, C3.2, C4.2, C5.1, C6.2, C7.1, IC1.4 (GND), J1.G1 (2), J1.G2 (2), J1.G3 (2), J1.G4 (2), JP2.2, Q2.1 (S_1), Q2.2 (S_2), Q2.3 (S_3), R1.1, R2.1, R3.2, R4.2, R15.2, R17.1, R30.2, U1.P$3 (GND), U1.P$8 (GND), U1.P$13 (GND), U1.P$18 (GND), U1.P$23 (GND), U1.P$28 (GND), U1.P$33 (GND), U1.P$38 (GND), U2.3 (GND), U2.12 (GND), U3.1 (GND), U3.2 (GND), U3.3 (GND), U3.4 (GND), U3.5 (GND), U3.11 (GND), U3.12 (GND), U3.20 (GND), U3.22 (GND)
/GPS_RESET: U1.P$22 (GP17), U2.10 (~RESET)
/GPS_RX: U1.P$6 (GP4), U2.1 (RXD)
/GPS_TX: U1.P$7 (GP5), U2.2 (TXD)
/GPS_WAKE_UP: U1.P$21 (GP16), U2.7 (WAKE_UP)
/G_DROGUE: Q2.4 (G), R30.1, R31.2
/LORA_BUSY: U1.P$16 (GP12), U3.14 (BUSY)
/LORA_CS: R1.2, U1.P$12 (GP9), U3.19 (NSS)
/LORA_DIO1: U1.P$19 (GP14), U3.13 (DIO1)
/LORA_MISO: U1.P$11 (GP8), U3.16 (MISO)
/LORA_MOSI: U1.P$15 (GP11), U3.17 (MOSI)
/LORA_RST: U1.P$17 (GP13), U3.15 (~RST)
/LORA_SCK: U1.P$14 (GP10), U3.18 (SCK)
/RXEN: U1.P$9 (GP6), U3.6 (RXEN)
/SCL: R3.1, U1.P$5 (GP3), U2.15 (I2C_SCL)
/SDA: R2.2, U1.P$4 (GP2), U2.16 (I2C_SDA)
/TXEN: U1.P$10 (GP7), U3.7 (TXEN)
/V_BATT: D1.2, JP2.1, LED1.A
unnamed: C1.1, IC1.6 (BST)
unnamed: C1.2, IC1.5 (SW), L1.1
unnamed: C4.1, D1.1, IC1.2 (EN), IC1.3 (VIN)
unnamed: LED1.C, R17.2
unnamed: LS2.N, R15.1
unnamed: Q5.1 (G), R4.1, R27.2
unnamed: LS2.P, Q5.2 (S)
unnamed: J1.1, U3.21 (ANT)

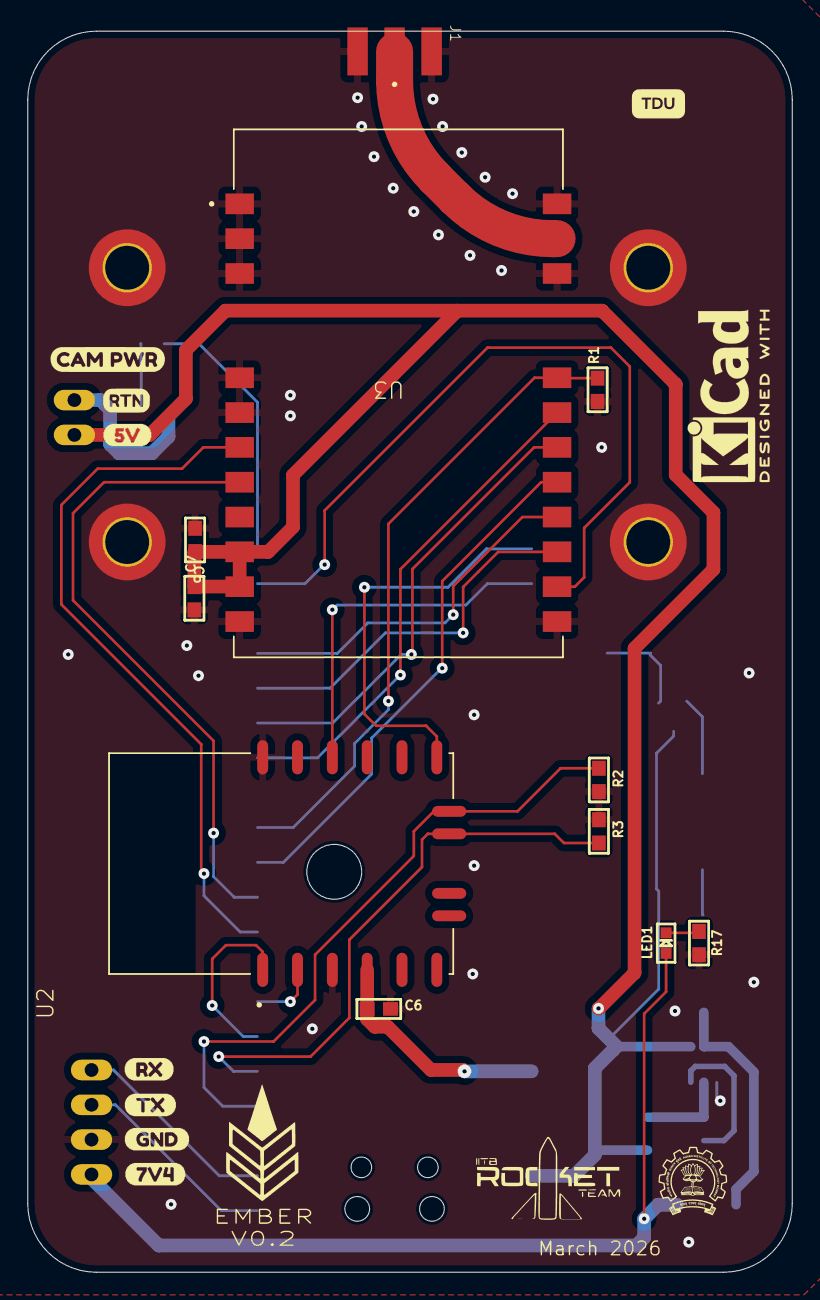
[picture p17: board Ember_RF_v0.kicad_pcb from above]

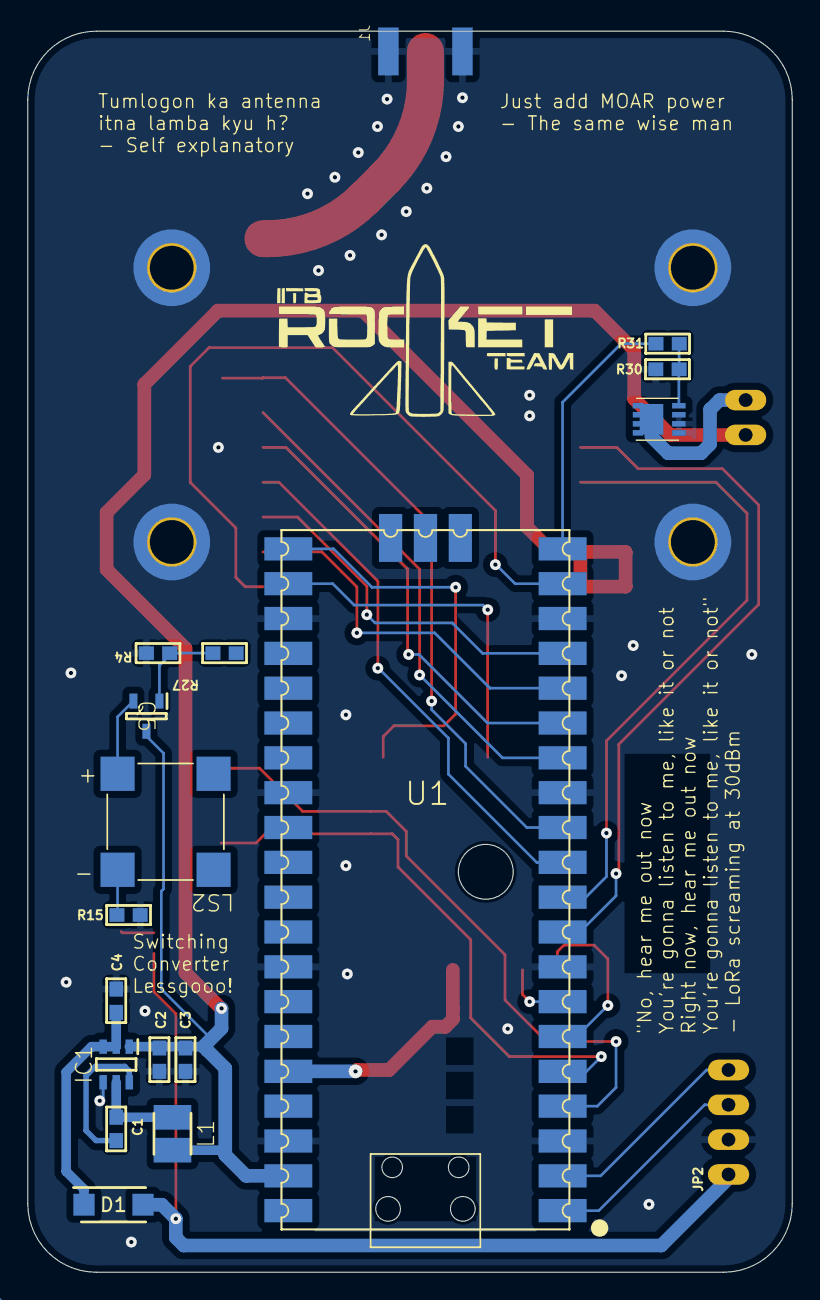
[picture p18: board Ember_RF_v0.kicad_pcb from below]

Board: 2 copper layers, 55.8 x 90.5 mm, 29 parts (18 on the bottom side), 33 nets.

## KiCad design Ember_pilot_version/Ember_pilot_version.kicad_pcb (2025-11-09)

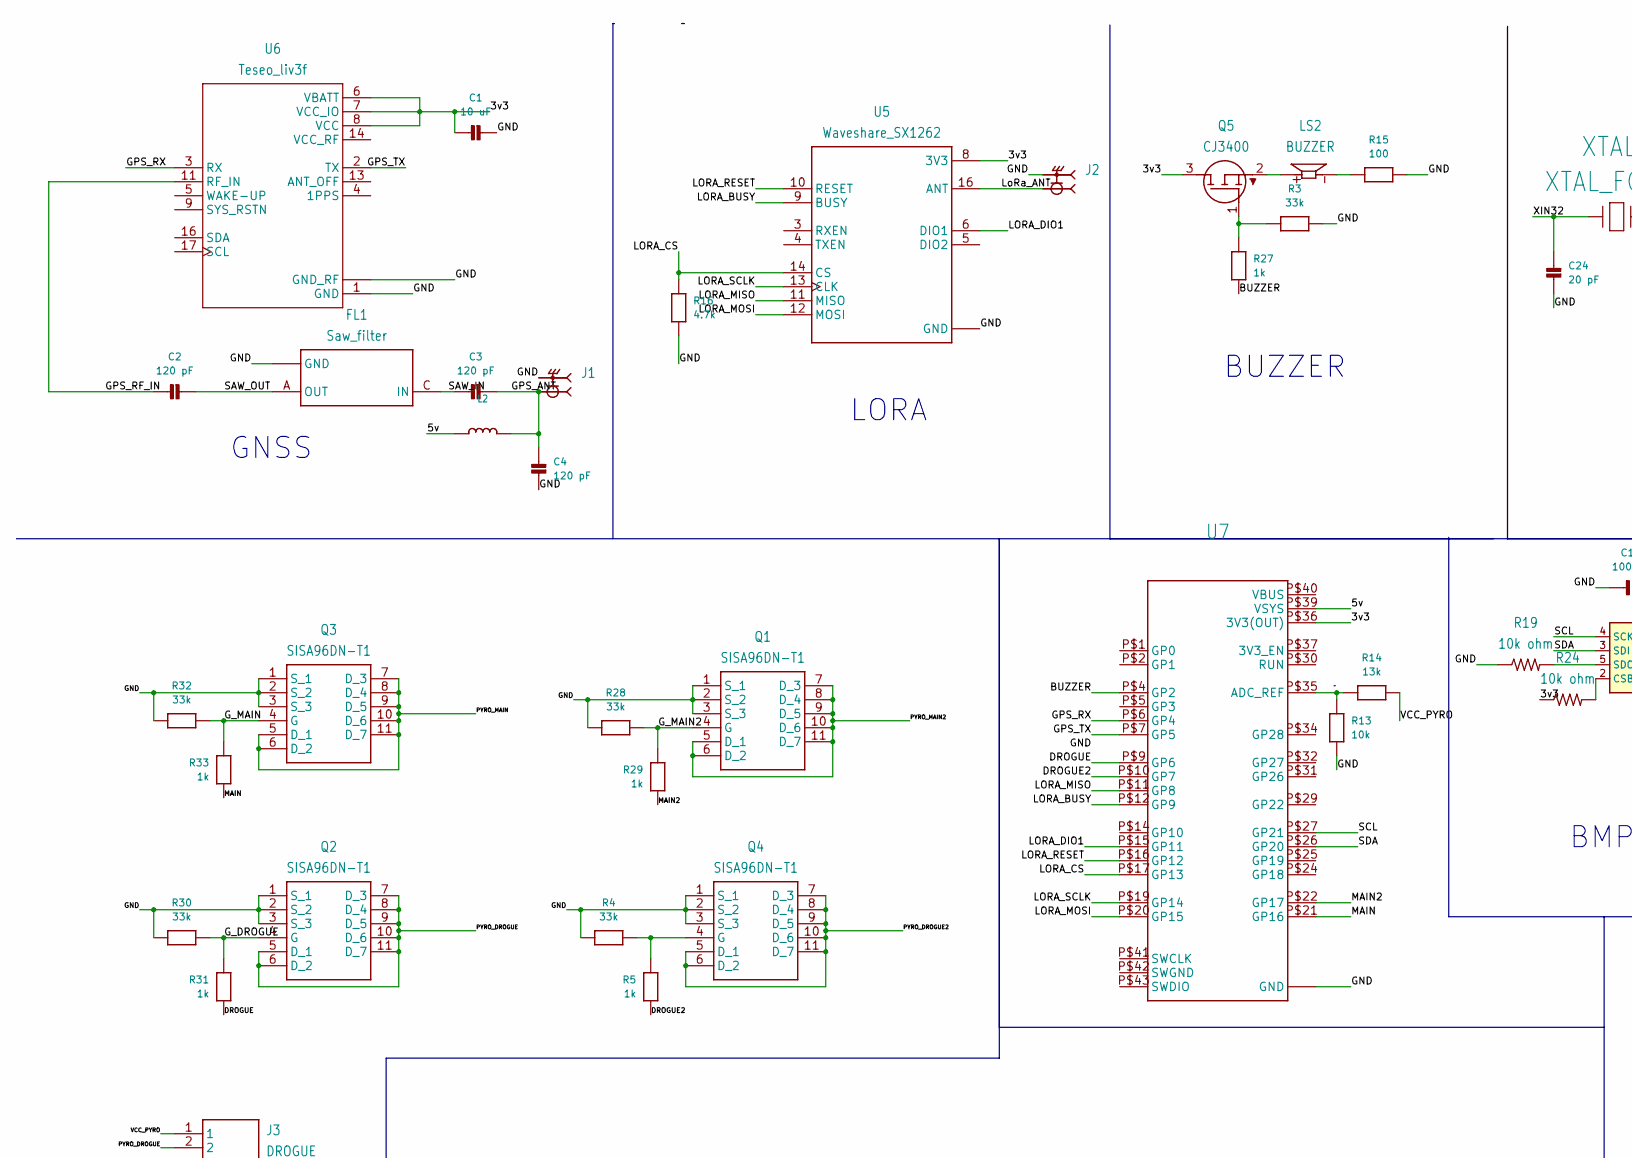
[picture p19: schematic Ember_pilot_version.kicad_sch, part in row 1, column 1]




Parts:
C1, C5, C6, C7: 10 uF; 0603
C2, C3, C4: 120 pF; 0603
C13, C14, C15: 100 nF; 0603
C16: 100nF; 0603
C24, C25: 20 pF; 0603
D2: RSX501LAM20TR; DIOM4725X105N; MOUSER_PART_NUMBER 755-RSX501LAM20TR; DigiKey_Part_Number RSX501LAM20CT-ND
FL1: Saw_filter; FIL_AFS14A04-1575.42-T3
J1, J2: RFSOLUTIONS_CON-SMA-EDGE-S
J3: DROGUE; ONSHORE_OSTTA020161
J4: BATT_CONN; AMASS_XT60-M
J5: MAIN; ONSHORE_OSTTA020161
J6: MAN2; ONSHORE_OSTTA020161
J7: DROGUE2; ONSHORE_OSTTA020161
J8: ARM; ONSHORE_OSTTA020161
L2: 0603
LED1: BATT_CONN; CHIPLED_0603
LS2: BUZZER; CUI_CMT-8530S-SMT
Q1, Q2, Q3, Q4: SISA96DN-T1; SIS862DNT1GE3
Q5: CJ3400; SOT95P240X115-3N
R1, R2, R19, R20, R21, R22, R23, R24: 10k ohm; R0603
R3, R4, R28, R30, R32: 33k; 0603
R5, R27, R29, R31, R33: 1k; 0603
R13: 10k; 0603
R14: 13k; 0603
R15, R17: 100; 0603
R16: 4.7k; 0603
U1: LDO Regulator 5v; SOT229P700X180-4N
U2: BNO055; LGA-28_5.2x3.8mm_P0.5mm
U3: LGA12_2X2X0P9_ROM
U4: BMP280; Bosch_LGA-8_2x2.5mm_P0.65mm_ClockwisePinNumbering
U5: Waveshare_SX1262; XCVR_CORE1262-868M
U6: Teseo_liv3f; TESEO-LIV3F
U7: PICO-PKG-SMD
XTAL1: XTAL_FC135; XTAL_FC-135_EPS

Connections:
/3v3: C1.2, C13.2, C14.1, C15.1, Q5.3 (D), R1.1, R2.1, R20.1, R21.1, R22.1, R24.1, U2.3 (VDD), U2.4 (~BOOT_LOAD_PIN), U2.28 (VDDIO), U3.1 (SDO/ADDR), U3.3 (IO_VDD), U3.7 (VDD), U3.10 (NCS), U4.6 (VDDIO), U4.8 (VDD), U5.8 (3V3), U6.6 (VBATT), U6.7 (VCC_IO), U6.8 (VCC), U7.P$36 (3V3(OUT))
/5v: C6.1, C7.1, L2.1, U1.2 (VOUT), U7.P$39 (VSYS)
/BATT_IN: D2.2, J4.P (POS)
/BUZZER: R27.1, U7.P$4 (GP2)
/DROGUE: R31.1, U7.P$9 (GP6)
/DROGUE2: R5.1, U7.P$10 (GP7)
/GND: C1.1, C4.1, C5.2, C6.2, C7.2, C13.1, C14.2, C15.2, C16.1, C24.1, C25.1, FL1.B (GND), FL1.D (GND), FL1.E (GND), J1.G1 (2), J1.G2 (2), J1.G3 (2), J1.G4 (2), J2.G1 (2), J2.G2 (2), J2.G3 (2), J2.G4 (2), J4.N (NEG), Q1.1 (S_1), Q1.2 (S_2), Q1.3 (S_3), Q2.1 (S_1), Q2.2 (S_2), Q2.3 (S_3), Q3.1 (S_1), Q3.2 (S_2), Q3.3 (S_3), Q4.1 (S_1), Q4.2 (S_2), Q4.3 (S_3), R3.2, R4.2, R13.1, R15.2, R16.1, R17.1, R19.1, R23.1, R28.2, R30.2, R32.2, U1.1 (GND/ADJ), U2.2 (GND), U2.5 (PS1), U2.6 (PS0), U2.18 (COM2), U2.25 (GNDIO), U3.4 (TRIG), U3.8 (GND_2), U3.9 (GND), U4.1 (GND), U4.7 (GND), U5.1 (GND), U5.2 (GND), U5.7 (GND), U5.15 (GND), U6.1 (GND), U6.10 (GND_RF), U6.12 (GND_RF), U7.P$3 (GND), U7.P$8 (GND), U7.P$13 (GND), U7.P$18 (GND), U7.P$23 (GND), U7.P$28 (GND), U7.P$33 (GND), U7.P$38 (GND)
/GPS_ANT: C3.1, C4.2, J1.1, L2.2
/GPS_RF_IN: C2.2, U6.11 (RF_IN)
/GPS_RX: R1.2, U6.3 (RX), U7.P$6 (GP4)
/GPS_TX: R2.2, U6.2 (TX), U7.P$7 (GP5)
/G_DROGUE: Q2.4 (G), R30.1, R31.2
/G_MAIN: Q3.4 (G), R32.1, R33.2
/G_MAIN2: Q1.4 (G), R28.1, R29.2
/LORA_BUSY: U5.9 (BUSY), U7.P$12 (GP9)
/LORA_CS: R16.2, U5.14 (CS), U7.P$17 (GP13)
/LORA_DIO1: U5.6 (DIO1), U7.P$15 (GP11)
/LORA_MISO: U5.11 (MISO), U7.P$11 (GP8)
/LORA_MOSI: U5.12 (MOSI), U7.P$20 (GP15)
/LORA_RESET: U5.10 (RESET), U7.P$16 (GP12)
/LORA_SCLK: U5.13 (CLK), U7.P$19 (GP14)
/LoRa_ANT: J2.1, U5.16 (ANT)
/MAIN: R33.1, U7.P$21 (GP16)
/MAIN2: R29.1, U7.P$22 (GP17)
/PYRO_DROGUE: J3.2, Q2.5 (D_1), Q2.6 (D_2), Q2.7 (D_3), Q2.8 (D_4), Q2.9 (D_5), Q2.10 (D_6), Q2.11 (D_7)
/PYRO_DROGUE2: J7.2, Q4.5 (D_1), Q4.6 (D_2), Q4.7 (D_3), Q4.8 (D_4), Q4.9 (D_5), Q4.10 (D_6), Q4.11 (D_7)
/PYRO_MAIN: J5.2, Q3.5 (D_1), Q3.6 (D_2), Q3.7 (D_3), Q3.8 (D_4), Q3.9 (D_5), Q3.10 (D_6), Q3.11 (D_7)
/PYRO_MAIN2: J6.2, Q1.5 (D_1), Q1.6 (D_2), Q1.7 (D_3), Q1.8 (D_4), Q1.9 (D_5), Q1.10 (D_6), Q1.11 (D_7)
/SAW_IN: C3.2, FL1.C (IN)
/SAW_OUT: C2.1, FL1.A (OUT)
/SCL: R21.2, U2.19 (COM1), U3.12 (SCLK/SCL), U4.4 (SCK), U7.P$27 (GP21)
/SDA: R20.2, U2.20 (COM0), U3.2 (SDI/SDA), U4.3 (SDI), U7.P$26 (GP20)
/VCC_PYRO: J3.1, J5.1, J6.1, J7.1, J8.1, R14.2
/V_BATT: C5.1, D2.1, J8.2, LED1.A, U1.3 (VIN)
/XIN32: C24.2, U2.27 (XIN32), XTAL1.1
/XOUT32: C25.2, U2.26 (XOUT32), XTAL1.2
unnamed: C16.2, U2.9 (CAP)
unnamed: LED1.C, R17.2
unnamed: LS2.N, R15.1
unnamed: Q4.4 (G), R4.1, R5.2
unnamed: Q5.1 (G), R3.1, R27.2
unnamed: LS2.P, Q5.2 (S)
unnamed: R23.2, U2.17 (COM3)
unnamed: R22.2, U2.11 (~RESET)
unnamed: R24.2, U4.2 (CSB)
unnamed: R19.2, U4.5 (SDO)
unnamed: R13.2, R14.1, U7.P$35 (ADC_REF)

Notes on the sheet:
KX134
GNSS
BUZZER
BNO055
PULL UPS
LORA
BMP280
Power Supply



Board: 4 copper layers, 75.0 x 83.0 mm, 62 parts (13 on the bottom side), 47 nets.

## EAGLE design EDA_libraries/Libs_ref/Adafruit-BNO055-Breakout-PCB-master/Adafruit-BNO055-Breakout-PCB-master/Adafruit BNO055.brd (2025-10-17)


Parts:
C1, C2: 22pF; 0805-NO
C3: 0.1uF; 0805-NO
C4: 0.1uF; 0805_10MGAP
C5: 10uF; 0805-NO
C6: 10uF; 0805_10MGAP
D1: 1n4148; SOD-323
FID1, FID2: FIDUCIAL""; FIDUCIAL_1MM
JP1: HEADER-1X676MIL; 1X06_ROUND_76
JP2: HEADER-1X476MIL; 1X04_ROUND_76
Q1, Q2: BSS138; SOT23-WIDE
R3, R4, R5, R6, R7, R10: 10K; 0805-NO
R8, R9: 10K; _0805MP
U1: MIC5225-3.3; SOT23-5
U$2, U$34: BNO055
U$29, U$30, U$31, U$32: MOUNTINGHOLE2.5_THICK; MOUNTINGHOLE_2.5_PLATED_THICK
Y1: 32.768kHz; CRYSTAL_8X3.8

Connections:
3.3V: C4.2, C6.1, JP1.2, Q1.1 (G), Q2.1 (G), R6.2, R7.2, R10.2, U1.5 (OUT), U$2.3 (VDD), U$2.4 (NBOOT_LOAD_PIN), U$2.28 (VDDIO)
5.0V: C5.1, JP1.1, R8.2, R9.2, U1.1 (IN), U1.3 (EN)
GND: C1.1, C2.1, C3.1, C4.1, C5.2, C6.2, JP1.3, R3.2, R4.2, R5.2, U1.2 (GND), U$2.2 (GND), U$2.10 (PIN10(GND)), U$2.15 (PIN15(GND)), U$2.16 (PIN16(GND)), U$2.18 (COM2(GND)), U$2.25 (GND)
I2CADDR_3V: JP2.4, R5.1, U$2.17 (COM3/I2C_ADDR)
INT_3V: JP2.3, U$2.14 (INT)
unnamed: C1.2, U$2.27 (XIN32), Y1.P$4 (2)
unnamed: C2.2, U$2.26 (XOUT32), Y1.P$1 (1)
unnamed: C3.2, U$2.9 (CAP)
NRESET_3V: D1.A, R10.1, U$2.11 (NRESET)
PS0_3V: JP2.1, R3.1, U$2.6 (PS0)
PS1_3V: JP2.2, R4.1, U$2.5 (PS1)
RST_5V: D1.C, JP1.6
SCL_3V: Q2.2 (S), R7.1, U$2.19 (COM1/SCL/RX)
SCL_5V: JP1.5, Q2.3 (D), R9.1
SDA_3V: Q1.2 (S), R6.1, U$2.20 (COM0/SDA/TX)
SDA_5V: JP1.4, Q1.3 (D), R8.1



Board: 2 copper layers, 57.7 x 31.8 mm, 32 parts (2 on the bottom side), 16 nets.

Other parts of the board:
U$3: PCBFEAT-REV-040
U$28: ADAFRUIT_TEXT_20MM
U$33: ADAFRUIT_2.5MM

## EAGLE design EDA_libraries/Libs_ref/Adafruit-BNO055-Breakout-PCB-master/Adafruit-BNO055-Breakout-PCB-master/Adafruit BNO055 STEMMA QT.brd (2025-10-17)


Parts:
C1, C2: 22pF; 0603-NO
C3, C9: 0.1uF; 0603-NO
C7, C8: 10uF; 0805-NO
CONN3, CONN4: STEMMA_I2C_QT; JST_SH4
D1: 1n4148; SOD-323
D2: GREEN; CHIPLED_0603_NOOUTLINE
FID3, FID4: FIDUCIAL_1MM
JP2: HEADER-1X476MIL; 1X04_ROUND_76
JP3: HEADER-1X670MIL; 1X06_ROUND_70
Q3: BSS138; SOT363
R1, R3: 10K; RESPACK_4X0603
R4: 10K; 0603-NO
SJ1: SOLDERJUMPER; SOLDERJUMPER_ARROW_NOPASTE
U2: AP2112K-3.3; SOT23-5
U$2: BNO055
U$45, U$46, U$48, U$49: MOUNTINGHOLE2.5; MOUNTINGHOLE_2.5_PLATED
X2: 32.768; XTAL3215

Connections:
3.3V: C8.1, C9.1, JP3.2, Q3.2 (G), Q3.5 (G), R1.1, R1.4 (1), R3.1, R4.1, SJ1.2, U2.5 (OUT), U$2.3 (VDD), U$2.4 (NBOOT_LOAD_PIN), U$2.8 (PIN8(SWCLK)), U$2.28 (VDDIO)
GND: C1.1, C2.1, C3.1, C7.2, C8.2, C9.2, CONN3.1 (GND), CONN3.MT1 (MT), CONN3.MT2 (MT), CONN4.1 (GND), CONN4.MT1 (MT), CONN4.MT2 (MT), D2.C, JP3.3, R3.2 (1), R3.5 (2), R3.6 (2), U2.2 (GND), U$2.2 (GND), U$2.10 (PIN10(GND)), U$2.15 (PIN15(GND)), U$2.16 (PIN16(GND)), U$2.18 (COM2(GND)), U$2.25 (GND)
I2CADDR_3V: JP2.2, R3.7 (2), SJ1.1, U$2.17 (COM3/I2C_ADDR)
INT_3V: JP2.1, U$2.14 (INT)
unnamed: C1.2, U$2.27 (XIN32), X2.P$2
unnamed: C2.2, U$2.26 (XOUT32), X2.P$1
unnamed: C3.2, U$2.9 (CAP)
unnamed: D2.A, R3.8 (2)
NRESET_3V: D1.A, R4.2, U$2.11 (NRESET)
PS0_3V: JP2.3, R3.3 (1), U$2.6 (PS0)
PS1_3V: JP2.4, R3.4 (1), U$2.5 (PS1)
RESET: D1.C, JP3.6
SCL: CONN3.4 (SCL), CONN4.4 (SCL), JP3.4, Q3.6 (D), R1.7 (2)
SCL_3V: Q3.1 (S), R1.5 (2), U$2.19 (COM1/SCL/RX)
SDA: CONN3.3 (SDA), CONN4.3 (SDA), JP3.5, Q3.3 (D), R1.6 (2)
SDA_3V: Q3.4 (S), R1.8 (2), U$2.20 (COM0/SDA/TX)
VCC: C7.1, CONN3.2 (V+), CONN4.2 (V+), JP3.1, R1.2 (1), R1.3 (1), U2.1 (IN), U2.3 (EN)

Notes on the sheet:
I2C Pullups & Shift
STEMMA/I2C Headers
ON LED
Power supply



Board: 2 copper layers, 25.4 x 20.3 mm, 30 parts (4 on the bottom side), 17 nets.

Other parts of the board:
U$51: ADAFRUIT_3.5MM
U$52: PCBFEAT-REV-040
U$53, U$54: STEMMAQT

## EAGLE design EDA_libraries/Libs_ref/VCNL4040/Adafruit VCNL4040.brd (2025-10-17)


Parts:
C1: 0.1uF; 0603-NO
C2, C3: 10uF; 0805-NO
CONN3, CONN4: STEMMA_I2C_QT; JST_SH4
D1: GREEN; CHIPLED_0603_NOOUTLINE
FID3, FID4: FIDUCIAL_1MM
JP1: HEADER-1X670MIL; 1X06_ROUND_70
Q2: BSS138; SOT363
R1: 10K; 0603-NO
R3: 10K; RESPACK_4X0603
U2: AP2112K-3.3; SOT23-5
U3: VCNL4040M3OE; VISHAY_VCNL4040_4X2X1.1
U$1, U$17, U$19, U$21: MOUNTINGHOLE2.5; MOUNTINGHOLE_2.5_PLATED

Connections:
3.3V: C1.1, C3.1, D1.A, JP1.2, Q2.2 (G), Q2.5 (G), R3.2 (1), R3.4 (1), U2.5 (OUT), U3.3 (VDD), U3.4 (VDD-LED)
CATHODE: U3.2 (C-SENSOR), U3.5 (C-LED)
GND: C1.2, C2.2, C3.2, CONN3.1 (GND), CONN4.1 (GND), JP1.3, R1.2, U2.2 (GND), U3.1 (GND)
INT: JP1.6, U3.6 (INT)
unnamed: D1.C, R1.1
SCL: CONN3.4 (SCL), CONN4.4 (SCL), JP1.4, Q2.6 (D), R3.8 (2)
SCL_3V: Q2.1 (S), R3.7 (2), U3.8 (SCL)
SDA: CONN3.3 (SDA), CONN4.3 (SDA), JP1.5, Q2.3 (D), R3.6 (2)
SDA_3V: Q2.4 (S), R3.5 (2), U3.7 (SDA)
VCC: C2.1, CONN3.2 (V+), CONN4.2 (V+), JP1.1, R3.1, R3.3 (1), U2.1 (IN), U2.3 (EN)

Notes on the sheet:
I2C Pullups & Shift
STEMMA/I2C Headers
ON LED
Power supply



Board: 2 copper layers, 25.4 x 17.8 mm, 22 parts (3 on the bottom side), 10 nets.

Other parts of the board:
U$22: ADAFRUIT_3.5MM
U$25: PCBFEAT-REV-040
U$30, U$31: STEMMAQT

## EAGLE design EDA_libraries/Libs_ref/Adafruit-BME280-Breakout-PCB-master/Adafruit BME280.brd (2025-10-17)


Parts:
C1, C3: 10uF; 0805-NO
D2: 1N4148; SOD-323
JP2: HEADER-1X770MIL; 1X07_ROUND_70
Q3, Q4: BSS138; SOT23-WIDE
R1, R2, R7, R8: 10K; 0805-NO
R4: 10K; _0805MP
U1: BME280
U2: MIC5225-3.3; SOT23-5
U$5, U$15: FIDUCIAL""; FIDUCIAL_1MM
U$7, U$8: MOUNTINGHOLE2.0; MOUNTINGHOLE_2.0_PLATED

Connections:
3.3V: C3.1, JP2.2, Q3.1 (G), Q4.1 (G), R1.2, R2.2, R4.2, U1.6 (VDDIO), U1.8 (VDD), U2.5 (OUT)
5.0V: C1.1, JP2.1, R7.2, R8.2, U2.1 (IN), U2.3 (EN)
CS_3V: D2.A, U1.2 (CSB)
CS_5V: D2.C, JP2.7
GND: C1.2, C3.2, JP2.3, U1.1 (GND), U1.7 (GND), U2.2 (GND)
SCK/SCL_5V: JP2.4, Q3.3 (D), R7.1
SCK_3V: Q3.2 (S), R2.1, U1.4 (SCK)
SDI/SDA_5V: JP2.6, Q4.3 (D), R8.1
SDI_3V: Q4.2 (S), R1.1, U1.3 (SDI)
SDO/ADR_3V: JP2.5, R4.1, U1.5 (SDO)

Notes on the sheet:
For SPI set CSB low at startup SDO=MISO, SDI=MOSI, SCK=SCK, CSB=CS/SSEL
For I2C leave CSB pulled high (default value) SDI=SDA, SCK=SCL
LEVEL SHIFTING (5V <--> 3V)



Board: 2 copper layers, 17.8 x 19.1 mm, 20 parts (2 on the bottom side), 10 nets.

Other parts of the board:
U$2, U$6: ADAFRUIT_2.5MM
U$20: PCBFEAT-REV-040

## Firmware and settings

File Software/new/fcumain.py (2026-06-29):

# =============================================================================
# FCU_main.py  –  Flight Computer Unit (FCU)
# RPi Pico 2
#
# Responsibilities:
#   - Read BNO055 (IMU), BMP280 (barometer), KX134 (high-G accel)
#   - Run state machine, pyro logic
#   - Log flight data to onboard flash
#   - Send packed telemetry frames to TDU over UART (B2B connector)
#   - Receive ACK from TDU over the same UART (handshake only)
#
# Nav algorithm moved to TDU. FCU no longer receives GPS packets.
# TDU owns: GPS (Quectel L89HA), nav Kalman filter, lat/lon/track.
#
# Pin assignments (from FCU schematic Ember_v0.2):
#   I2C-0  : SDA=GP20  SCL=GP21  (BNO055 0x28, BMP280 0x76, KX134 0x1F,
#                                  ADS1115 0x48)
#   BNO_INT: GP18  (interrupt, not used in firmware yet)
#   KX_INT : GP19  (interrupt, not used in firmware yet)
#   Buzzer : GP2   (via MOSFET, passive PWM)
#   LED    : GP25  (onboard Pico LED)
#   LEDs   : GP0 (nav light A), GP1 (nav light B)
#   Pyros  : DROGUE=GP6  DROGUE2=GP7  MAIN=GP16  MAIN2=GP17
#   B2B    : UART-0  TX=GP4  RX=GP5  (to TDU)
#   ADC_REF: GP35
#   PYRO CONTINUITY:
#     GP26 (ADC0) = PYRO_DROGUE  (primary)
#     GP27 (ADC1) = PYRO_MAIN    (primary)
#   ADS1115 (U5, I2C-0, 0x48):
#     AIN0 = differential pressure probe  →  volt_dp
#     AIN1 = not connected
#     AIN2 = PYRO_MAIN2   (redundant)     →  volt_main2
#     AIN3 = PYRO_DROGUE2 (redundant)     →  volt_drogue2
#
# Packet formats:
#
#   B2B_FMT  '<si18f'  77 bytes  — sent to TDU over UART every 200 ms
#     'F' | t_ms(i) | state | temp
#     | bno ax ay az | gx gy gz | kx ax ay az
#     | alt | vel
#     | volt_drogue_primary | volt_main_primary
#     | volt_main2 | volt_drogue2 | dp
#
#   LOG_FMT  '<si19f'  81 bytes  — written to flash during flight
#     'L' | t_ms(i) | state | temp
#     | bno ax ay az | gx gy gz | kx ax ay az
#     | alt | vel
#     | volt_drogue_primary | volt_main_primary
#     | volt_dp | volt_main2 | volt_drogue2 | dp
#
# State machine:
#   UNARMED → FLIGHT_READY → BOOST → COAST → DROGUE → MAIN → LANDED
#
# Startup handshake (blocking, before async loop):
#   FCU → TDU : b'FCU_INIT_OK\n'                 every 100 ms until ACK
#   TDU → FCU : b'TDU_ACK\n'                     unblocks FCU
#   FCU runs  : _calib_bmp(), then sets calib_time
#   FCU → TDU : b'C' + calib_alt(f) + calib_temp(f)   9 bytes
# =============================================================================

from machine import I2C, Pin, UART, PWM, ADC, freq
from math   import sqrt, pi
from time   import ticks_ms, sleep_ms
from ulab   import numpy as np
from bno055_base import BNO055_BASE
from bno055 import *
import ustruct
import uasyncio as asyncio
import uos
import gc
import micropython

# ── optional high-G accel ────────────────────────────────────────────────────
try:
    from kx132 import KX132, ACC_RANGE_16
    KX_AVAILABLE = True
except ImportError:
    KX_AVAILABLE = False

# ── optional barometer ───────────────────────────────────────────────────────
try:
    from bmp280 import BMP280
    BMP_AVAILABLE = True
except ImportError:
    BMP_AVAILABLE = False

# ── optional ADS1115 ─────────────────────────────────────────────────────────
try:
    import ads1x15
    ADS_AVAILABLE = True
except ImportError:
    ADS_AVAILABLE = False

micropython.alloc_emergency_exception_buf(100)
gc.collect()
freq(150_000_000)


# =============================================================================
# Clash Royale fanfare
# =============================================================================
def play_clash_royale(buzzer: PWM):
    buzzer.duty_u16(0)
    C5      = 523;  D5  = 587;  F5  = 698
    Fsharp5 = 740;  G5  = 784;  Gsharp5 = 831
    A5      = 880;  Asharp5 = 932;  Csharp5 = 554
    C6      = 1047; F6  = 1397

    melody  = [Csharp5, Fsharp5, Gsharp5, C6, F6]
    tempo   = [14,      14,      14,      14,  6]
    melody1 = [Asharp5, A5, F5, G5, D5, C5]
    tempo1  = [4,       10, 12, 12,  8,  6]

    def play(mel, tmp):
        for i in range(len(mel)):
            buzzer.freq(mel[i])
            buzzer.duty_u16(32000)
            sleep_ms(1000 // tmp[i])
            buzzer.duty_u16(0)
            sleep_ms(20)

    play(melody, tempo)
    sleep_ms(1000)
    play(melody1, tempo1)
    buzzer.duty_u16(0)


# =============================================================================
# BNO055
# =============================================================================
class BNO055(BNO055_BASE):
    pass


# =============================================================================
# FCU
# =============================================================================
class FCU:

    G = 9.80665

    # ── States ────────────────────────────────────────────────────────────────
    STATE_UNARMED      = 0
    STATE_FLIGHT_READY = 1
    STATE_BOOST        = 2
    STATE_COAST        = 3
    STATE_DROGUE       = 4
    STATE_MAIN         = 5
    STATE_LANDED       = 6

    # ── Board-to-board telemetry (UART → TDU) ─────────────────────────────────
    # 'F' | t_ms(i) | state(f) | temp(f)
    # | bno ax ay az(3f) | gx gy gz(3f) | kx ax ay az(3f)
    # | alt(f) | vel(f)
    # | volt_drogue_primary(f) | volt_main_primary(f)
    # | volt_main2(f) | volt_drogue2(f) | dp(f)
    # = 1s + 1i + 18f = 77 bytes
    B2B_FMT = '<si18f'
    B2B_LEN = ustruct.calcsize(B2B_FMT)   # 77 bytes

    # ── Flash log format ──────────────────────────────────────────────────────
    # 'L' | t_ms(i) | state(f) | temp(f)
    # | bno ax ay az(3f) | gx gy gz(3f) | kx ax ay az(3f)
    # | alt(f) | vel(f)
    # | volt_drogue_primary(f) | volt_main_primary(f)
    # | volt_dp(f) | volt_main2(f) | volt_drogue2(f)
    # | dp(f) | airspeed(f)
    # = 1s + 1i + 20f = 85 bytes
    LOG_FMT = '<si19f'
    LOG_LEN = ustruct.calcsize(LOG_FMT)   # 81 bytes

    # ── Calibration packet ────────────────────────────────────────────────────
    # 'C' | calib_alt(f) | calib_temp(f)   → 9 bytes
    CALIB_FMT = '<s2f'
    CALIB_LEN = ustruct.calcsize(CALIB_FMT)

    # ── Pyro continuity thresholds ────────────────────────────────────────────
    PYRO_CONT_THRESHOLD = int(1.2 / 3.3 * 65535)   # ~23831 counts  (Pico ADC)
    ADS_CONT_THRESHOLD  = 1.2                        # volts          (ADS1115)
    PYRO_CONT_DURATION  = 3500                       # ms

    def __init__(self):
        self.state      = self.STATE_UNARMED
        self.t_log      = 0
        self.last_t_log = 0
        self.async_loop = None
        self.calib_time = 0

        self.bno = None
        self.bmp = None
        self.kx  = None
        self.ads = None
        self.b2b = None

        # ── Primary pyro continuity (Pico ADC) ───────────────────────────────
        # GP26 = PYRO_DROGUE   GP27 = PYRO_MAIN
        self.adc_pyro_drogue = None
        self.adc_pyro_main   = None

        self.volt_drogue_primary = 0.0
        self.volt_main_primary   = 0.0

        self.cont_ch1 = False   # drogue (GP26)
        self.cont_ch2 = False   # main   (GP27)

        # ── Redundant pyro continuity + airspeed (ADS1115) ───────────────────
        # AIN0 = diff pressure   AIN2 = PYRO_MAIN2   AIN3 = PYRO_DROGUE2
        self.volt_dp = 0.0
        self.volt_main2    = 0.0
        self.volt_drogue2  = 0.0

        self.cont_main2   = False
        self.cont_drogue2 = False

        self.ADS_ADDR    = 0x48
        self.ADS_RATE    = 7      # ads1x15 rate for set_conv — 860 SPS
        self.ads_working = False

        self.both_cont_since = 0

        # Beep queue: push (n, t_ms, freq) from any async context.
        # beep_task drains it without blocking the loop.
        self._beep_queue = []

        self.drogue_pin  = None
        self.drogue2_pin = None
        self.main_pin    = None
        self.main2_pin   = None

        self.buzzer = None
        self.led    = None
        self.led0   = None
        self.led1   = None

        self.bno_scale = 1.0
        self.kx_scale  = 1.0
        self.temp      = 0.0
        self.alt       = 0.0
        self.density   = 1.15

        # ── Rocket-frame sensor scalars ───────────────────────────────────────
        # BNO055 (Ember V0.2):
        #   axial (+up) = -BNO Y   lateral Y = BNO Z   lateral Z = BNO X
        # Gyro (rad/s):
        #   roll = -BNO gyro Y   pitch = BNO gyro Z   yaw = BNO gyro X
        # KX134:
        #   axial (+up) = KX X   lateral Y = KX Z   lateral Z = KX Y
        self.ax    = 0.0;  self.ay    = 0.0;  self.az    = 0.0
        self.gx    = 0.0;  self.gy    = 0.0;  self.gz    = 0.0
        self.kx_ax = 0.0;  self.kx_ay = 0.0;  self.kx_az = 0.0

        self.calib_altitude = 0.0
        self.calib_temp     = 0.0
        self.calib_count    = 0

        self.buf_len = 10
        self.alt_buf = np.zeros((self.buf_len,))
        self.vel_buf = np.zeros((self.buf_len,))
        self.acc_buf = np.zeros((self.buf_len,))

        self.t_events = [0.0] * 6

        # Two separate buffers — one for B2B, one for flash log
        self.data_b2b    = bytearray(self.B2B_LEN)
        self.data_log    = bytearray(self.LOG_LEN)
        self.data_buffer = bytearray(0)   # pre-launch rolling buffer (LOG frames)
        self.data_file   = None
        self.index       = 0
        self.size        = 0

        storage         = uos.statvfs('/')
        self.free_bytes = storage[0] * storage[3]
        self.logging_done = False

        # ── Flight parameters ─────────────────────────────────────────────────
        self.liftoff_accel             = 2.0
        self.min_liftoff_alt           = 10
        self.force_burnout_time        = 5000
        self.lockout_drogue_time       = 16000
        self.force_drogue_time         = 26000
        self.main_alt                  = 400
        self.drogue_to_main_lockout    = 60000
        self.ballistic_lockout_time    = 6000
        self.max_re_entry_speed        = -60.0
        self.touchdown_alt             = 50
        self.touchdown_vel_limit       = 0.1
        self.main_to_touchdown_lockout = 10000
        self.runtime                   = 36000000

        # ── Sensor calibration ───────────────────────────────────────────────
        # Differential pressure sensor supply voltage.
        # Datasheet: V_OUT = V_S * (0.009 * P_kPa + 0.04)
        # Tune if your 5V rail reads slightly off (±0.1V typical).
        self.VS_SUPPLY                 = 5.0   # V

        self.bno_working = True
        self.bmp_working = True
        self.kx_working  = True
        self.tdu_ready   = False
        self._flicker_event = False

    # ── altitude ──────────────────────────────────────────────────────────────
    def altitude(self):
        return 4947.19 * (8.9611 - pow(self.bmp.pressure, 0.190255))

    def rho(self, y):
        return (
            pow(8.9611 - (y + self.calib_altitude) / 4947.19, 5.2479)
            / (78410.439 + 287.06 * self.calib_temp - 1.86589 * (y + self.calib_altitude))
        )

    # ── failure logger ────────────────────────────────────────────────────────
    def failure(self, e):
        try:
            if self.free_bytes - self.size > 1000:
                with open('fcu_fail.txt', 'a') as f:
                    f.write(str(self.t_log) + ',' + str(e) + '\n')
        except Exception:
            pass

    # ── beeper (blocking — init context only) ─────────────────────────────────
    def beep(self, n=1, t=75, f=2000):
        self.buzzer.freq(f)
        for _ in range(n):
            self.buzzer.duty_u16(30000)
            sleep_ms(t)
            self.buzzer.duty_u16(0)
            if n > 1:
                sleep_ms(t)

    def beep_flight_ready(self):
        for frq in (2000, 3000, 4000):
            self.buzzer.freq(frq)
            self.buzzer.duty_u16(30000)
            sleep_ms(80)
            self.buzzer.duty_u16(0)
            sleep_ms(40)

    # ── async beep consumer ───────────────────────────────────────────────────
    async def beep_task(self):
        while True:
            if self._beep_queue:
                n, t, f = self._beep_queue.pop(0)
                self.buzzer.freq(f)
                for i in range(n):
                    self.buzzer.duty_u16(30000)
                    await asyncio.sleep_ms(t)
                    self.buzzer.duty_u16(0)
                    if i < n - 1:
                        await asyncio.sleep_ms(t)
            else:
                await asyncio.sleep_ms(20)

    # =========================================================================
    # Hardware init
    # =========================================================================
    def init_hardware(self):
        print('[FCU] Hardware init start')

        # ── GPIO ─────────────────────────────────────────────────────────────
        self.led    = Pin(25, Pin.OUT)
        self.led0   = Pin(0,  Pin.OUT);  self.led0.value(0)
        self.led1   = Pin(1,  Pin.OUT);  self.led1.value(0)
        self.buzzer = PWM(Pin(2));       self.buzzer.duty_u16(0)

        self.drogue_pin  = Pin(6,  Pin.OUT);  self.drogue_pin.value(0)
        self.drogue2_pin = Pin(7,  Pin.OUT);  self.drogue2_pin.value(0)
        self.main_pin    = Pin(16, Pin.OUT);  self.main_pin.value(0)
        self.main2_pin   = Pin(17, Pin.OUT);  self.main2_pin.value(0)

        # ── Primary pyro continuity ADC ───────────────────────────────────────
        self.adc_pyro_drogue = ADC(Pin(26))   # GP26 = PYRO_DROGUE
        self.adc_pyro_main   = ADC(Pin(27))   # GP27 = PYRO_MAIN
        print('[FCU] Pyro ADC ready (GP26=DROGUE, GP27=MAIN)')

        # ── UART to TDU ───────────────────────────────────────────────────────
        self.b2b = UART(1, baudrate=115200, tx=Pin(4), rx=Pin(5))
        print('[FCU] B2B UART ready')

        # ── I2C-0 ─────────────────────────────────────────────────────────────
        sleep_ms(200)
        i2c0 = I2C(0, scl=Pin(21), sda=Pin(20), freq=400_000)
        _devs = []
        for _attempt in range(3):
            _devs = i2c0.scan()
            if _devs:
                break
            print('[FCU] I2C scan empty, retrying ({})...'.format(_attempt + 1))
            sleep_ms(200)
        print('[FCU] I2C devices: {}'.format([hex(d) for d in _devs]))

        # ── BMP280 ────────────────────────────────────────────────────────────
        if BMP_AVAILABLE:
            try:
                self.bmp = BMP280(i2c0)
                print('[FCU] BMP280 OK')
            except Exception as e:
                print('[FCU] BMP280 FAIL:', e)
                self.failure('BMP280 init: ' + str(e))

        # ── BNO055 ────────────────────────────────────────────────────────────
        try:
            self.bno = BNO055(i2c0)
            self.bno.mode(0)
            sleep_ms(25)
            bno_offsets = bytearray(
                b'\xef\xff\t\x00\xef\xff\xae\x03\xa2\xff\x98\x04'
                b'\xff\xff\x02\x00\xff\xff\xe8\x03\x02\x03'
            )
            ACCEL_OFFSET_X_LSB = 0x55
            for i in range(6):
                self.bno._write(ACCEL_OFFSET_X_LSB + i, bno_offsets[i])
            self.bno._write(0x67, bno_offsets[18])
            self.bno._write(0x68, bno_offsets[19])
            sleep_ms(25)
            self.bno.mode(7)
            sleep_ms(20)
            print('[FCU] Place IMU at rest for scale cal')
            self.bno_scale = 0.0
            for _ in range(10):
                ba = (0.0, 0.0, 0.0)
                while ba == (0.0, 0.0, 0.0):
                    ba = self.bno.accel()
                    sleep_ms(1)
                self.bno_scale += self.G / sqrt(ba[0]**2 + ba[1]**2 + ba[2]**2) / 10
            print('[FCU] BNO055 OK  scale={:.4f}'.format(self.bno_scale))
        except Exception as e:
            print('[FCU] BNO055 FAIL:', e)
            self.failure('BNO055 init: ' + str(e))
            self.bno_working = False

        # ── KX134 ─────────────────────────────────────────────────────────────
        if KX_AVAILABLE:
            try:
                self.kx = KX132(i2c0, address=0x1F)
                self.kx.acc_range = ACC_RANGE_16
                self.kx_scale = 0.0
                for _ in range(10):
                    ka = (0.0, 0.0, 0.0)
                    while ka == (0.0, 0.0, 0.0):
                        ka = self.kx.acceleration
                        sleep_ms(1)
                    self.kx_scale += self.G / sqrt(ka[0]**2 + ka[1]**2 + ka[2]**2) / 10
                print('[FCU] KX134 OK  scale={:.4f}'.format(self.kx_scale))
            except Exception as e:
                print('[FCU] KX134 FAIL:', e)
                self.failure('KX134 init: ' + str(e))
                self.kx_working = False

        # ── ADS1115 ───────────────────────────────────────────────────────────
        # AIN0=diff_pressure  AIN2=PYRO_MAIN2  AIN3=PYRO_DROGUE2
        if ADS_AVAILABLE:
            try:
                self.ads = ads1x15.ADS1115(i2c0, self.ADS_ADDR)
                self.ads_working = True
                print('[FCU] ADS1115 OK (0x{:02X})'.format(self.ADS_ADDR))
            except Exception as e:
                print('[FCU] ADS1115 FAIL:', e)
                self.failure('ADS1115 init: ' + str(e))
                self.ads_working = False

        # ── Index file ────────────────────────────────────────────────────────
        try:
            with open('/index.txt', 'r') as f:
                self.index = int(f.read())
        except Exception:
            self.index = 0
        with open('/index.txt', 'w') as f:
            f.write(str(self.index + 1))

        print('[FCU] Hardware init complete')
        play_clash_royale(self.buzzer)

        # ── Wait for TDU ACK ──────────────────────────────────────────────────
        print('[FCU] Waiting for TDU ACK...')
        while True:
            self.b2b.write(b'FCU_INIT_OK\n')
            sleep_ms(100)
            rx = self.b2b.read(64)
            if rx and b'TDU_ACK' in rx:
                print('[FCU] TDU ACK received')
                self.tdu_ready = True
                break

        # ── BMP calibration ───────────────────────────────────────────────────
        self._calib_bmp()
        self.calib_time = ticks_ms()
        print('[FCU] calib_time set: {} ms from boot'.format(self.calib_time))

        # ── Send calibration data to TDU ──────────────────────────────────────
        calib_pkt = ustruct.pack(self.CALIB_FMT, b'C',
                                 self.calib_altitude, self.calib_temp)
        self.b2b.write(calib_pkt)
        print('[FCU] Sent calib: alt={:.1f}m  T={:.1f}°C'.format(
            self.calib_altitude, self.calib_temp))

    # ── BMP calibration ───────────────────────────────────────────────────────
    def _calib_bmp(self, n=10):
        if self.bmp is None:
            return
        try:
            self.calib_temp = self.bmp.temperature
            avg = 0.0
            for _ in range(n):
                avg += self.altitude()
                sleep_ms(10)
            self.calib_altitude = avg / n
            self.calib_count += 1
            print('[FCU] Calib alt={:.1f}m  T={:.1f}°C'.format(
                self.calib_altitude, self.calib_temp))
        except Exception as e:
            self.calib_altitude = 0.0
            self.failure('BMP calib: ' + str(e))

    # =========================================================================
    # Async tasks
    # =========================================================================

    async def blink(self, t):
        while True:
            self.led.value(0)
            await asyncio.sleep_ms(t)
            self.led.value(1)
            await asyncio.sleep_ms(t)

    async def led_flicker(self):
        async def strobe_normal(led, offset_ms):
            await asyncio.sleep_ms(offset_ms)
            while True:
                if self.state >= self.STATE_DROGUE:
                    await asyncio.sleep_ms(100)
                    continue
                led.value(1); await asyncio.sleep_ms(70)
                led.value(0); await asyncio.sleep_ms(100)
                led.value(1); await asyncio.sleep_ms(70)
                led.value(0); await asyncio.sleep_ms(1760)

        async def strobe_slow():
            while True:
                if self.state == self.STATE_DROGUE:
                    self.led0.value(1); self.led1.value(0)
                    await asyncio.sleep_ms(500)
                    self.led0.value(0)
                    await asyncio.sleep_ms(1500)
                elif self.state >= self.STATE_MAIN:
                    self.led0.value(1); self.led1.value(1)
                    await asyncio.sleep_ms(500)
                    self.led0.value(0); self.led1.value(0)
                    await asyncio.sleep_ms(1500)
                else:
                    await asyncio.sleep_ms(100)

        async def event_watcher():
            while True:
                if self._flicker_event:
                    self._flicker_event = False
                    for _ in range(6):
                        self.led0.value(1); self.led1.value(1)
                        await asyncio.sleep_ms(40)
                        self.led0.value(0); self.led1.value(0)
                        await asyncio.sleep_ms(40)
                await asyncio.sleep_ms(10)

        self.async_loop.create_task(strobe_normal(self.led0, 0))
        self.async_loop.create_task(strobe_normal(self.led1, 1000))
        self.async_loop.create_task(strobe_slow())
        self.async_loop.create_task(event_watcher())
        await asyncio.sleep(0)

    # ── sensor read loop ──────────────────────────────────────────────────────
    async def get_data(self):
        last_beep = 0
        sleep_ms(10)

        while True:
            self.t_log = ticks_ms() - self.calib_time
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

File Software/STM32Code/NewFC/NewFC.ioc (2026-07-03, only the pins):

Mcu.UserName=STM32F411CEUx
PA10.Signal=USART1_RX
PA13.Signal=SYS_JTMS-SWDIO
PA14.Signal=SYS_JTCK-SWCLK
PA5.Signal=SPI1_SCK
PA6.Signal=SPI1_MISO
PA7.Signal=SPI1_MOSI
PA9.Signal=USART1_TX
PB6.Signal=I2C1_SCL
PB7.Signal=I2C1_SDA
PC14-OSC32_IN.Signal=RCC_OSC32_IN
PC15-OSC32_OUT.Signal=RCC_OSC32_OUT

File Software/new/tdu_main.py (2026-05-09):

# =============================================================================
# TDU_main.py  –  Telemetry & Data Unit (TDU)
# RPi Pico 2
#
# Responsibilities:
#   - Receive packed telemetry frames from FCU over UART (B2B connector)
#   - Parse GPS (NMEA) from onboard GPS module
#   - Echo GPS fix back to FCU over B2B UART
#   - Forward combined telemetry + GPS over LoRa SX1262 to ground station
#   - Optionally control camera trigger output (GP15 / GP20)
#   - Play Angry Birds jingle AFTER FCU sends FCU_INIT_OK
#   - Drive drogue camera-ignition pyro output (G_DROGUE via SISA96DN-T1)
#
# Pin assignments (from TDU schematic Ember_RF_v0):
#   B2B UART  : UART-0  TX=GP0  RX=GP1       (from/to FCU)
#   GPS I2C   : SDA=GP2  SCL=GP3             (for LC86G config only, not NMEA)
#   GPS UART  : UART-1  TX=GP4  RX=GP5       (NMEA stream)
#   GPS RESET : GP17
#   GPS WAKE  : GP16
#   LoRa SPI  : LORA_SCK=GP10  LORA_MOSI=GP11  LORA_MISO=GP8
#               LORA_CS=GP9   LORA_RST=GP13   LORA_DIO1=GP14  LORA_BUSY=GP12
#   Buzzer    : GP18  (via Q5 NPN transistor, active HIGH)
#   Camera    : GP15  (CAM trigger via Q2 SISA96DN-T1)
#   G_DROGUE  : SISA96DN-T1 gate on GP20   (camera/secondary drogue, "CAM")
#   LED       : GP25  (onboard)
# =============================================================================

from machine import UART, Pin, PWM, I2C
from time    import ticks_ms, sleep_ms
import ustruct
import uasyncio as asyncio
import gc
import micropython

from sx1262 import SX1262     # sx1262.py + sx126x.py + _sx126x.py must be on TDU

micropython.alloc_emergency_exception_buf(100)
gc.collect()


# =============================================================================
# Angry Birds jingle  (plays on TDU after FCU_INIT_OK is received)
# Taken directly from angrybird.py
# =============================================================================
NOTES = {
    'REST': 0,
    'C5':  523, 'CS5': 554, 'D5':  587, 'DS5': 622, 'E5':  659,
    'F5':  698, 'FS5': 740, 'G5':  784, 'GS5': 831, 'A5':  880,
    'AS5': 932, 'B5':  988, 'C6': 1047, 'CS6':1109, 'D6': 1175,
    'DS6':1245, 'E6': 1319, 'F6': 1397, 'FS6':1480, 'G6': 1568,
}

ANGRY_BIRDS_MELODY = [
    ('E5',  1), ('FS5', 1), ('G5', 2),  ('E5',  2),
    ('B5',  1), ('REST',1),
    ('E5',  1), ('FS5', 1), ('G5', 2),  ('B5',  2),
    ('B5',  1), ('REST',3),
    ('B5',  1), ('C6',  1), ('B5', 1),  ('A5',  1),
    ('G5',  2), ('G5',  1), ('FS5',1),  ('E5',  1),
]


def play_angry_birds(buzzer: PWM, tempo: int = 140):
    beat_ms = int(60000 / tempo / 4)
    for note, dur in ANGRY_BIRDS_MELODY:
        freq = NOTES.get(note, 0)
        ms   = beat_ms * dur
        if freq == 0:
            buzzer.duty_u16(0)
        else:
            buzzer.freq(freq)
            buzzer.duty_u16(32768)
        sleep_ms(ms)
        buzzer.duty_u16(0)
        sleep_ms(20)
    buzzer.duty_u16(0)


# =============================================================================
# GPS helpers  (from gps_test2.py)
# =============================================================================
def _validate_checksum(sentence: str) -> bool:
    if '*' not in sentence:
        return False
    try:
        data, chk = sentence[1:].split('*', 1)
    except ValueError:
        return False
    calc = 0
    for c in data:
        calc ^= ord(c)
    return '{:02X}'.format(calc) == chk.strip().upper()


def _nmea_to_decimal(raw: str, direction: str):
    if not raw:
        return None
    try:
        dot = raw.index('.')
        degrees = int(raw[:dot - 2])
        minutes = float(raw[dot - 2:])
    except (ValueError, IndexError):
        return None
    dec = degrees + minutes / 60.0
    if direction in ('S', 'W'):
        dec = -dec
    return dec


def _parse_rmc(parts):
    if len(parts) < 10 or parts[2] != 'A':
        return None
    lat = _nmea_to_decimal(parts[3], parts[4])
    lon = _nmea_to_decimal(parts[5], parts[6])
    if lat is None or lon is None:
        return None
    return {
        'lat':      lat,
        'lon':      lon,
        'speed_kn': parts[7],
        'heading':  float(parts[8]) if parts[8] else 0.0,
        'time':     parts[1],
        'date':     parts[9],
    }


def _parse_gga(parts):
    if len(parts) < 15:
        return None
    try:
        if not parts[6] or int(parts[6]) == 0:
            return None
    except ValueError:
        return None
    return {
        'fix_quality': int(parts[6]),
        'num_sats':    parts[7],
        'hdop':        float(parts[8]) if parts[8] else 99.0,
        'altitude_m':  float(parts[9]) if parts[9] else 0.0,
    }


# =============================================================================
# LoRa over-air telemetry frame
#
# Ground station receives:
#   b'T' | t_ms(i32) | state(i8) | temp(f) | ax(f) | ay(f) | az(f)
#   | gx(f) | gy(f) | gz(f) | alt(f) | vel(f) | lat(f) | lon(f) | heading(f)
#   = 1 + 4 + 1 + 12*4 = 54 bytes
# =============================================================================
LORA_FMT = '!ci12f'
LORA_LEN = ustruct.calcsize(LORA_FMT)

# FCU telemetry frame format (must match FCU_main.py TELEM_FMT)
FCU_FMT = '!ci17f'
FCU_LEN = ustruct.calcsize(FCU_FMT)

# GPS echo to FCU:  b'G' + lat(f) + lon(f) + heading(f) = 13 bytes
GPS_ECHO_FMT = '!cfff'
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

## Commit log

2025-10-11 Added KiCad project file
    [Ember_v1.0.kicad_pcb, Ember_v1.0.kicad_sch]
2025-10-17 Added the libraries
    [Adafruit BME280.brd, Adafruit BME280.sch, Adafruit BNO055 STEMMA QT.brd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]
2025-10-19 Added power supply
    [Ember_v1.0.kicad_sch, RSX501LAM20TR.step]
2025-10-19 Added the flash, XTAL remaining
    [Ember_v1.0.kicad_sch]
2025-10-19 Added xtal
    [Ember_v1.0.kicad_sch]
2025-10-21 Sensors done, some issues to be resolved
    [Ember_v1.0.kicad_sch]
2025-10-23 crystal error resolved
    [Ember_v1.0.kicad_pcb, Ember_v1.0.kicad_sch]
2025-10-23 Added pilot board
    [Ember_pilot_version.kicad_pcb, Ember_pilot_version.kicad_sch, Ember_v1.0.kicad_sch]
2025-10-24 gnss added
    [Ember_pilot_version.kicad_sch]
2025-10-25 LoRa, Buck converter and pyro (partially) added
    [Ember_pilot_version.kicad_sch]
2025-10-30 Added Final Iterations in pilot version
    [Ember_pilot_version.kicad_sch]
2025-10-31 changed buzzer circuit, pyro mosfets and finalized connections
    [Ember_pilot_version.kicad_sch]
2025-10-31 issues resolved
    [Ember_pilot_version.kicad_sch]
2025-11-02 routing started
    [Ember_pilot_version.csv, Ember_pilot_version.kicad_pcb, Ember_pilot_version.kicad_sch]
2025-11-03 initial layout done, rf traces remaining
    [Ember_pilot_version.kicad_pcb, Ember_pilot_version.kicad_sch, project_logo.dxf]
2025-11-04 RF traces done with some design changes
    [Ember_pilot_version.kicad_pcb, Ember_pilot_version.kicad_sch]
2025-11-04 A few slight changes
    [Ember_pilot_version.kicad_pcb]
2025-11-04 Optimized routings
    [Ember_pilot_version.kicad_pcb]
2025-11-08 board finalised
    [Ember_pilot_version.kicad_pcb]
2025-11-09 corrected some missed issues
    [Ember_pilot_version.kicad_pcb]
2025-12-08 power supply changes to LDO
    [Ember_v1.0.kicad_sch]
2025-12-08 Updated hirarchy and structure
    [Ember_v1.0.kicad_sch, main.kicad_sch, rf_board.kicad_sch]
2025-12-25 Base requirements added in schemcatics
    [Ember_v1.0.kicad_pcb, main.kicad_sch]
2026-02-02 Added everything till test launch 1 prep
    [Ember_pilot_version.csv, Ember_v1.0.kicad_pcb, main.kicad_sch]
2026-02-12 Added Ember_v0.2
    [Ember_v0.2.kicad_pcb, Ember_v0.2.kicad_sch]
2026-02-14 Roughly added the strain gauge thingy
    [Ember_v0.2.kicad_sch]
2026-02-14 Added the files for RF board
    [Ember_RF_v0.kicad_pcb, Ember_RF_v0.kicad_sch]
2026-03-09 anything until test launch prep
    [Ember_RF_v0.kicad_sch, Ember_v0.2.kicad_sch]
2026-03-19 all until 19 mar
    [Ember_RF_v0.kicad_sch, Ember_v0.2.kicad_sch]
2026-03-21 Ember V0.2 routing halfway done
    [Ember_v0.2.kicad_pcb, Ember_v0.2.kicad_sch]
2026-03-21 Ahaan's RF Headers 16 to 4
    [Ember_RF_v0.kicad_sch]
2026-03-22 RF Board PCB Attempt 1
    [Ember_RF_v0.kicad_pcb, Ember_RF_v0.kicad_sch]
2026-03-22 main board routing started
    [Ember_v0.2.kicad_pcb, Ember_v0.2.kicad_sch]
2026-03-23 Some corrections done and main board routing halfway done
    [Ember_RF_v0.kicad_sch, Ember_v0.2.kicad_pcb, Ember_v0.2.kicad_sch]
2026-03-25 Some changes on V0.2 layout
    [Ember_v0.2.kicad_pcb, Ember_v0.2.kicad_sch]
2026-03-27 board route almost complete
    [Ember_v0.2.kicad_pcb, Ember_v0.2.kicad_sch]
2026-03-27 did some graphic things on silkscreen
    [Ember_v0.2.kicad_pcb]
2026-03-28 Added some assets and V0.2 is sent for review
    [Ember_v0.2.kicad_pcb]
2026-03-28 All relevant DRC errors are resolved
    [Ember_v0.2.kicad_pcb, Ember_v0.2.kicad_sch]
2026-03-28 All routings completed, Lisan Al-gaib!
    [Ember_RF_v0.kicad_pcb, Ember_RF_v0.kicad_sch, Ember_v0.2.kicad_pcb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]
2026-03-30 TDU board LDO is replaced by AP63205
    [Ember_RF_v0.kicad_pcb, Ember_RF_v0.kicad_sch]
2026-03-30 All changes and things are done in both FCU and TDU - Lisan Al-gaib!
    [Ember_RF_v0.kicad_pcb, Ember_RF_v0.kicad_sch, Ember_v0.2.kicad_pcb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]
2026-04-01 v0.2 and RF v0 sent for fab - Lisan Al-gaib
    [Ember_RF_v0.kicad_pcb, Ember_RF_v0.kicad_sch, Ember_v0.2.kicad_pcb]
2026-06-26 Added the irec 2026 fcu data
    [IREC_2026_ANANTA_FCU.csv]

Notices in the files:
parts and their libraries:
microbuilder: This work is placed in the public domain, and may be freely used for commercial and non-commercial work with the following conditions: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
